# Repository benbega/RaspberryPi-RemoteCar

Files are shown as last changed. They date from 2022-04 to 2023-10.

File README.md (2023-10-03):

# RaspberryPi-RemoteCar
Repository hosting code for my RC car project based on the Raspberry Pi 4B+

## **Introduction**

This is a remote controlled car based on two Raspberry Pi 4B+ single board computers. The car chassis is from an old kit for collegiate competitions that I got for free from my university electronics stockroom. The car is powered by 2 7V DC motors, capable of approximately 23,000 RPM without a load.

A more robust document with project details will be posted as a PDF in this repository soon, containing a list of the exact hardware being used and instructions to setup the project yourself.

[A video of the project's current state can be found by clicking here](https://youtu.be/IsMrb5jVGqQ) 

## **Car Setup**

The car portion of the project contains a chassis, two DC motors, a servo, a Raspberry Pi 4B+, and a custom PCB. The PCB was fully custom designed, and incorporates an L293D motor driver chip, as well as indicator LEDs, signal pins for the servo, and hookups for the system's battery. The car uses a small 7V battery to power all of the microelectronic components, as well as a 5V 3A battery pack to power the Raspberry Pi. Although the dual battery system is extremely heavy and inefficient, it was chosen to suit the Raspberry Pi's high current demands.

The design files and information about the custom PCB can be found in the RaspiCar_PCB2 folder in this GitHub repository.

## **Wireless Communication**

The wireless controller functionality is implemented by utilizing the Raspberry Pi's remote GPIO functionality through the gpiozero library. The Raspberry Pi powering the controller is setup to be a wireless access point, which the car's Raspberry Pi connects to automatically upon boot. This allows the Remote GPIO setup to work anywhere, not just in specific locations that have a prexisting WiFi network. While lower power Raspberry Pi models, or microcointrollers could likely be used to accomplish the same functionality, these are the boards I currently have, and there is no reason currently to change the design.

## **State of the Project**

The project is currently in a complete state, where all systems are functional as originally designed. The car is able to freely drive and steer, and starts in a driveable state upon boot. The car is heavier than originally designed due to the Raspberry Pi power supply, so the top speed is relatively low.

## **Looking Forward**

I do not currently have plans to update this project, as I am focusing on something else I will write about soon, but in the future my goal is to switch out the motors and servo for significantly more powerful options, and utilize a more efficient LiPo battery pack. A related near term project I plan on completing is a short, detailed write up on how the Raspberry Pi Remote GPIO is setup, as I think it is one of the more interesting aspects of the overall design.

--

This project is licensed under the terms of the MIT license

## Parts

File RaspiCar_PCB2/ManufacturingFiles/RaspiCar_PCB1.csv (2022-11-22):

Source: | D:\KiCadProjects\RaspiCar_PCB2\RaspiCar_PCB1.kicad_sch
Date: | 10/15/2022 9:34:41 PM
Tool: | Eeschema (6.0.4)
Generator: | C:\Program Files\KiCad\6.0\bin\scripting\plugins/bom_csv_grouped_by_value_with_fp.py
Component Count: | 17
Ref | Qnty | Value | Cmp name | Footprint | Description | Vendor
C1, C2, | 2 | 1uF | C | Capacitor_SMD:C_Elec_5x5.4 | Unpolarized capacitor
H1, H2, H3, H4, | 4 | MountingHole | MountingHole | MountingHole:MountingHole_2.2mm_M2 | Mounting Hole without connection
L293D1, | 1 | L293D | L293D | Package_DIP:DIP-16_W7.62mm | Quadruple Half-H Drivers
LED1, | 1 | LED1 | LED | LED_THT:LED_D5.0mm | Light emitting diode
LED2, | 1 | LED2 | LED | LED_THT:LED_D5.0mm | Light emitting diode
Motor_1, | 1 | MotorTerminal1 | Screw_Terminal_01x02 | TerminalBlock:TerminalBlock_Altech_AK300-2_P5.00mm | Generic screw terminal, single row, 01x02, script generated (kicad-library-utils/schlib/autogen/connector/)
Motor_2, | 1 | MotorTerminal2 | Screw_Terminal_01x02 | TerminalBlock:TerminalBlock_Altech_AK300-2_P5.00mm | Generic screw terminal, single row, 01x02, script generated (kicad-library-utils/schlib/autogen/connector/)
PWR_GND1, | 1 | PWR_GND | Conn_01x02_Male | Connector_PinHeader_2.54mm:PinHeader_1x02_P2.54mm_Vertical | Generic connector, single row, 01x02, script generated (kicad-library-utils/schlib/autogen/connector/)
R1, R2, | 2 | 3.3k | R | Resistor_THT:R_Axial_DIN0207_L6.3mm_D2.5mm_P7.62mm_Horizontal | Resistor
Raspi_Logic1, | 1 | PiLogicHeaders | Conn_01x06_Male | Connector_PinHeader_2.54mm:PinHeader_1x06_P2.54mm_Vertical | Generic connector, single row, 01x06, script generated (kicad-library-utils/schlib/autogen/connector/)
Raspi_PWR1, | 1 | RaspiPWR/GND | Conn_01x02_Male | Connector_PinHeader_2.54mm:PinHeader_1x02_P2.54mm_Vertical | Generic connector, single row, 01x02, script generated (kicad-library-utils/schlib/autogen/connector/)
ServoPWR1, | 1 | ServoPWR/GND | Conn_01x02_Male | Connector_PinHeader_2.54mm:PinHeader_1x02_P2.54mm_Vertical | Generic connector, single row, 01x02, script generated (kicad-library-utils/schlib/autogen/connector/)

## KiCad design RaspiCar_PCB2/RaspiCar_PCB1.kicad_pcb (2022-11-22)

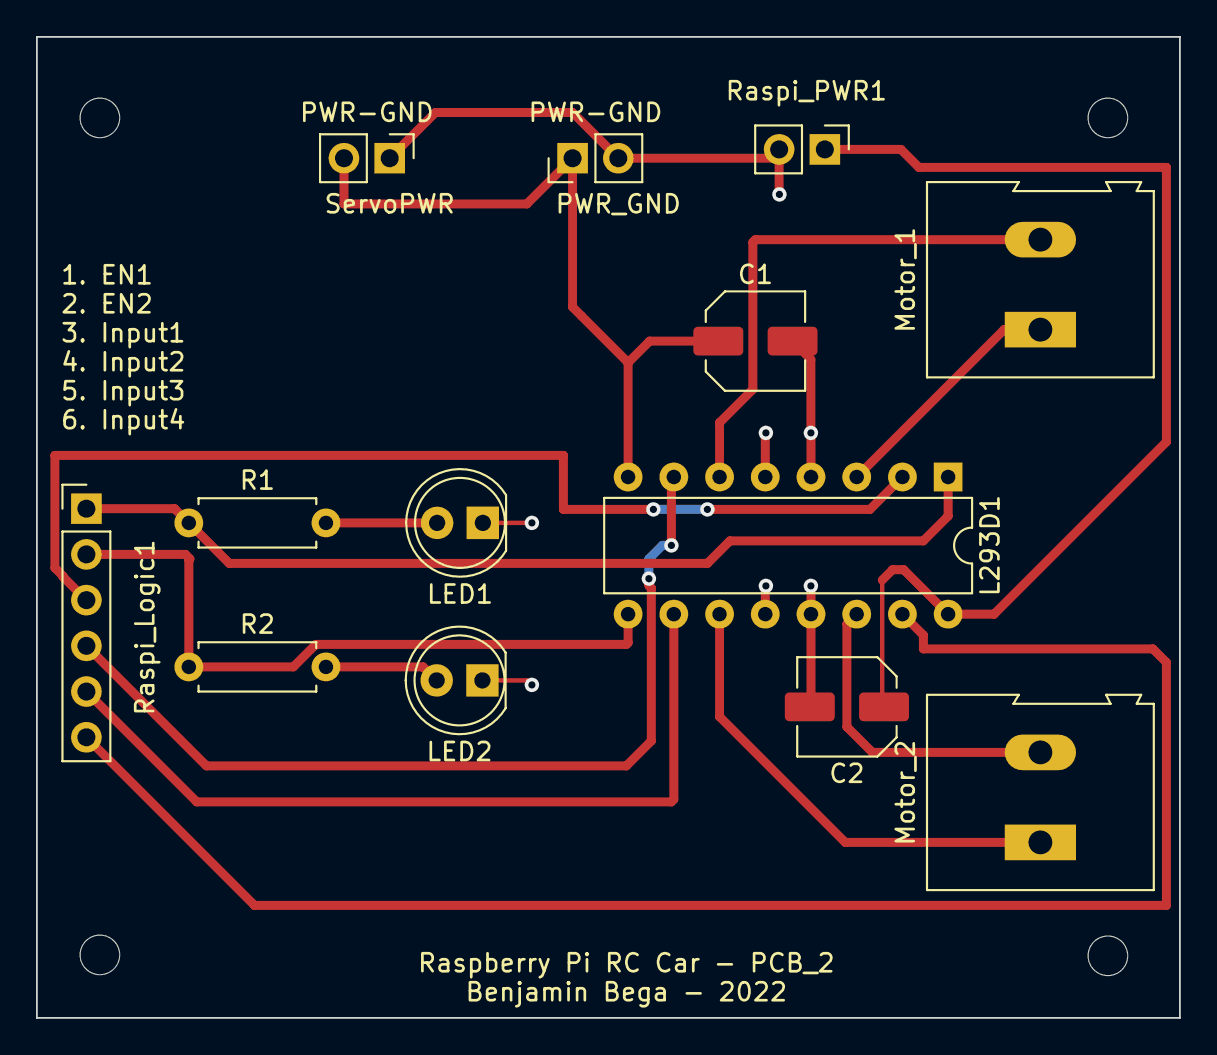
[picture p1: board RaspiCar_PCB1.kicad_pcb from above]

Board: 2 copper layers, 63.5 x 54.5 mm, 17 parts (0 on the bottom side), 15 nets.

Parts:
C1, C2: 1uF; C_Elec_5x5.4
H1, H2, H3, H4: MountingHole; MountingHole_2.2mm_M2
L293D1: L293D; DIP-16_W7.62mm
LED1: LED1; LED_D5.0mm
LED2: LED2; LED_D5.0mm
Motor_1: MotorTerminal1; TerminalBlock_Altech_AK300-2_P5.00mm
Motor_2: MotorTerminal2; TerminalBlock_Altech_AK300-2_P5.00mm
PWR_GND: PWR_GND; PinHeader_1x02_P2.54mm_Vertical
R1, R2: 3.3k; R_Axial_DIN0207_L6.3mm_D2.5mm_P7.62mm_Horizontal
Raspi_Logic1: PiLogicHeaders; PinHeader_1x06_P2.54mm_Vertical
Raspi_PWR1: RaspiPWR/GND; PinHeader_1x02_P2.54mm_Vertical
ServoPWR: ServoPWR/GND; PinHeader_1x02_P2.54mm_Vertical

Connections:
+5V: C2.1, L293D1.16 (VCC1), Raspi_PWR1.1
+7.5V: C1.1, L293D1.8 (VCC2), PWR_GND.1, ServoPWR.2
GND: C1.2, C2.2, L293D1.4 (GND), L293D1.5 (GND), L293D1.12 (GND), L293D1.13 (GND), LED1.1 (K), LED2.1 (K), PWR_GND.2, Raspi_PWR1.2, ServoPWR.1
unnamed: L293D1.1 (EN1,2), R1.1, Raspi_Logic1.1
unnamed: L293D1.2 (1A), Raspi_Logic1.3
unnamed: L293D1.3 (1Y), Motor_1.1
unnamed: L293D1.6 (2Y), Motor_1.2
unnamed: L293D1.7 (2A), Raspi_Logic1.4
unnamed: L293D1.9 (EN3,4), R2.1, Raspi_Logic1.2
unnamed: L293D1.10 (3A), Raspi_Logic1.5
unnamed: L293D1.11 (3Y), Motor_2.1
unnamed: L293D1.14 (4Y), Motor_2.2
unnamed: L293D1.15 (4A), Raspi_Logic1.6
unnamed: LED1.2 (A), R1.2
unnamed: LED2.2 (A), R2.2

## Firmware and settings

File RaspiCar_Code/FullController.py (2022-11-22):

# Full controller script, including throttle and steering control

import gpiozero as gp
from gpiozero.pins.rpigpio import RPiGPIOFactory
from time import sleep

#Local Pin Variables
localFactory = RPiGPIOFactory() #gets local pin instances

lm = gp.Motor(23,24,pwm=True); # Left Motor in1/in2
rm = gp.Motor(27,22,pwm=True); # Right motor in3/4
servo = gp.Servo(5)

throttle = gp.RotaryEncoder(17, 18, pin_factory=localFactory, max_steps=20, wrap=False)
    # Rotary encoder for throttle. 20 steps for throttle, LOCAL PIN
steer = gp.RotaryEncoder(22, 23, pin_factory=localFactory, max_steps=20, wrap=False)
    # Rotary encoder for throttle. 20 steps for throttle, LOCAL PIN

lmEnable = gp.LED(25); #EnablePin1
rmEnable = gp.LED(13); #EnablePin2
lmEnable.on(); #enable left motor
rmEnable.on(); #enable right motor

try:
    while(True):
        throttleVal = throttle.value*20
        steerVal = steer.value*20
        if(steerVal > 0):
            print("Going right, steer: ", steerVal)
            scaledSteer = ((steerVal)*5)/100
            servo.value = scaledSteer
            print("Scaled steer: ", scaledSteer)
            
        elif(steerVal == 0):
            print("Going straight")
            servo.value = 0
            
        elif(steerVal < 0):
            print("Going left, steer: ", steerVal)
            scaledSteer = ((steerVal)*5)/100
            servo.value = scaledSteer
            print("Scaled steer: ", scaledSteer)
            
            
            
        if(throttleVal > 0):
            #going forward
            lmEnable.on()
            rmEnable.on()
            print("Going forward, throttle: ", throttleVal)
            scaledThrottle = ((throttleVal)*5)/100
            lm.forward(scaledThrottle)
            rm.forward(scaledThrottle)
            print("Scaled throttle: ", scaledThrottle)
            
        elif(throttleVal == 0):
            print("Throttle off - stopping")
            lmEnable.off()
            rmEnable.off()
            
        elif(throttleVal < 0):
            lmEnable.on()
            rmEnable.on()
            print("Going backward, throttle: ", throttleVal)
            scaledThrottle = (abs((throttleVal))*5)/100
            lm.backward(scaledThrottle)
            rm.backward(scaledThrottle)
            print("Scaled throttle: ", scaledThrottle)
            
finally:
    print("closing")

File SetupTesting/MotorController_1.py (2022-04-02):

# Test motor controller script for single motor.
# Proves connection between Raspberry Pis using Remote GPIO via gpiozero
# Increases speed of left motor going forward, then reverses. 

#### Usage
##
#### $ GPIOZERO_PIN_FACTORY=pigpio PIGPIO_ADDR=<IP address of Pi to be controlled> python3 MotorController_1.py
##
####
import gpiozero as gp
from time import sleep

lm = gp.Motor(24,23,pwm=True); # Left Motor in1/in2

lmEnable = gp.LED(25); #Bridge enable PIN
lmEnable.on(); #enable left motor

while(True):
    print("front front front")
    for x in range(50, 100):#Incrementally increases speed of left motor, forwards
        lm.forward(x/100);
        sleep(0.1)
        
    for x in range(100, 50):
        #Incrementally decreases speed of left motor to avoid harsh changes in direction
        lm.forward(x/100);
        sleep(0.1)
        
    print("back back back") 
    for y in range(50, 100):#Incrementally increases speed of left motor, backwards
        lm.backward(y/100)
        sleep(0.1)
        
    for y in range(100, 50):
        #Incrementally decreases speed of left motor to avoid harsh changes in direction
        lm.backward(y/100)
        sleep(0.1)
        
gp.close()#cleanly closes GPIO

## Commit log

2022-04-02 Added MotorController Test Script
2022-10-03 CarPCB Commit
    Includes files for the PCB, version 1
    [RaspiCar_PCB1-B_Cu.gbr, RaspiCar_PCB1-B_Mask.gbr, RaspiCar_PCB1-B_Paste.gbr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]
2022-11-22 RaspiCar_0.2
    Added second PCB revision and full controller code
    [RaspiCar_PCB1-B_Cu.gbr, RaspiCar_PCB1-B_Mask.gbr, RaspiCar_PCB1-B_Paste.gbr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]
2023-03-03 Fixed folder names and ReadMe
    [FullController.py]
